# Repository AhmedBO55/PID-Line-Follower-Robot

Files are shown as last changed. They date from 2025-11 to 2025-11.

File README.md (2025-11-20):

# PID Line Follower Robot
##  Project Overview
PID Line Follower Robot is a project with the objective to understand the line follower concept and PID system. It’s an affordable version of a competitive robot, and v0; the next version will have better components and a PCB design.

91e5619f-f241-466d-bc85-fe74e6d3bd5d
---
## Why ?
I did this project because I am very interested in robotics competitions, and I want to create my own line follower robot and compete with it in future competitions. This is why I started this project: to understand the fundamentals before buying fancy components. I decided to make my mistakes now, and I am willing to learn and create a PCB in the future for this project.

{8EE49D31-0FA8-4DDD-9549-9236D85A650A}

68747470733a2f2f626c75657072696e742e6861636b636c75622e636f6d2f757365722d6174746163686d656e74732f626c6f62732f70726f78792f65794a66636d467062484d694f6e73695a474630595349364e7a49774e79776963485679496a6f69596d
---
## Circuit diagram

Circuit diagram

--- 

## Features
- **PID control** for smooth and accurate line following 
- **Real-time PID tuning** via a web page hosted by the robot
- **3D-printed chassis** adapted for the BFD-1000  
- **Bluetooth test mode** for quick motor debugging
  
{E63CA688-48E1-4CCD-8186-648663711028}

---
##  How It Works
1-The BFD-1000 reads the position of the line. 

2-The ESP32 computes an error value from the sensor readings. 

3-A PID algorithm generates the correction output.  

4-The TB6612FNG driver adjusts each motor’s speed. 

5-The robot’s Wi-Fi interface allows live tuning of Kp, Ki, and Kd values. 

---
## BOM (Bill of Materials)
I've created a BOM for the components used in this project. I didn’t include the cost and source links of the vendors, as I live in Tunisia and prices are not like the rest of the world, and our shops are not international.
But I've included the description and notes to explain the use of each component. If you want to change any of them, feel free to do so.

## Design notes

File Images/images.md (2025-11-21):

## 📸 Project Images
--- 
### 🔹 Previous Version (Summer of Making)
68747470733a2f2f626c75657072696e742e6861636b636c75622e636f6d2f757365722d6174746163686d656e74732f626c6f62732f70726f78792f65794a66636d467062484d694f6e73695a474630595349364e6a6b334f43776963485679496a6f69596d

---
### 🔹 Line Follower with QTR Sensor (Old Prototype)

314ee7e9-e2c3-470f-afe7-d1aa61988d41
91e5619f-f241-466d-bc85-fe74e6d3bd5d
68747470733a2f2f626c75657072696e742e6861636b636c75622e636f6d2f757365722d6174746163686d656e74732f626c6f62732f70726f78792f65794a66636d467062484d694f6e73695a474630595349364f446b344f43776963485679496a6f69596d
68747470733a2f2f626c75657072696e742e6861636b636c75622e636f6d2f757365722d6174746163686d656e74732f626c6f62732f70726f78792f65794a66636d467062484d694f6e73695a474630595349364f446b344e79776963485679496a6f69596d
68747470733a2f2f626c75657072696e742e6861636b636c75622e636f6d2f757365722d6174746163686d656e74732f626c6f62732f70726f78792f65794a66636d467062484d694f6e73695a474630595349364e7a63314d43776963485679496a6f69596d
68747470733a2f2f626c75657072696e742e6861636b636c75622e636f6d2f757365722d6174746163686d656e74732f626c6f62732f70726f78792f65794a66636d467062484d694f6e73695a474630595349364e7a63304f53776963485679496a6f69596d
68747470733a2f2f626c75657072696e742e6861636b636c75622e636f6d2f757365722d6174746163686d656e74732f626c6f62732f70726f78792f65794a66636d467062484d694f6e73695a474630595349364e7a63304f43776963485679496a6f69596d

### 🔹 Final Line Follower Robot (With BFD-1000) 

314ee7e9-e2c3-470f-afe7-d1aa61988d41
91e5619f-f241-466d-bc85-fe74e6d3bd5d
b005e480-9caa-4929-82fe-6bf18c532cd6

## 🧩 CAD Models

### 🔹 CAD V1 (Old 3D Model)
{86EB5DD3-BE2E-442E-AB9C-22109B1CB365}

### 🔹 CAD V2 (Updated model for BFD-1000)

{8EE49D31-0FA8-4DDD-9549-9236D85A650A}

## 🔌 Electronics & Circuit
Circuit diagram

68747470733a2f2f626c75657072696e742e6861636b636c75622e636f6d2f757365722d6174746163686d656e74732f626c6f62732f70726f78792f65794a66636d467062484d694f6e73695a474630595349364e7a49774e79776963485679496a6f69596d

68747470733a2f2f626c75657072696e742e6861636b636c75622e636f6d2f757365722d6174746163686d656e74732f626c6f62732f70726f78792f65794a66636d467062484d694f6e73695a474630595349364e7a49774f43776963485679496a6f69596d

5562393c-81c9-4ac4-81d2-6645e74e5eff

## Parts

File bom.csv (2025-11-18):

Item | Description | Quantity | Notes
ESP32 Dev Board | Main microcontroller | 1 | Handles PID
BFD-1000 Line Sensor | 6-channel IR line detection module | 1 | Primary sensor for line following
TB6612FNG Motor Driver | Dual H-bridge motor driver | 1 | Controls both N20 motors with PWM
N20 Gear Motors | 6V DC gear motors | 2 | Main motors for movement
N20 Motor Brackets | 3D printed or metal holders | 2 | Motor mounting
Ball Caster (Bille Libre) | Front support wheel | 1 | Helps robot balance and glide
L7805 Voltage Regulator | 5V linear regulator | 1 | Provides 5V for sensors and logic
Lithium Battery (or 18650 pack) | Main power source | 1 | Used to power motors + electronics
Battery Holder or Case | For securing the battery | 1 | Depending on your battery type
Switch | On/Off power switch | 1 | Main power control
Prototype Board / Custom PCB | Your soldered board or final PCB | 1 | Main circuit assembly
JST / Dupont Cables | Connection wires | As needed | For sensors,motors and power
3D Printed Chassis | Your custom robot frame | 1 | Designed to fit ESP32 + BFD-1000
Wheels | Compatible with N20 motors | 2 | Main driving wheels
Standoffs & Screws | M3 or M2 hardware set | As needed | For assembling chassis and PCB
USB Cable | For flashing ESP32 | 1 | Used during development
Soldering Supplies | Solder,flux,wires | 1 set | For assembling the board

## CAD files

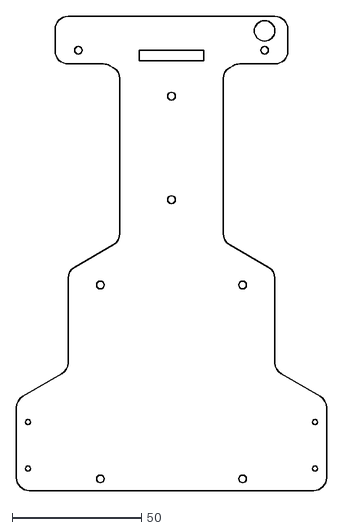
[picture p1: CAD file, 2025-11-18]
CAD/DXF/V2/Line follower robot DXF.dxf
120.0 x 183.4

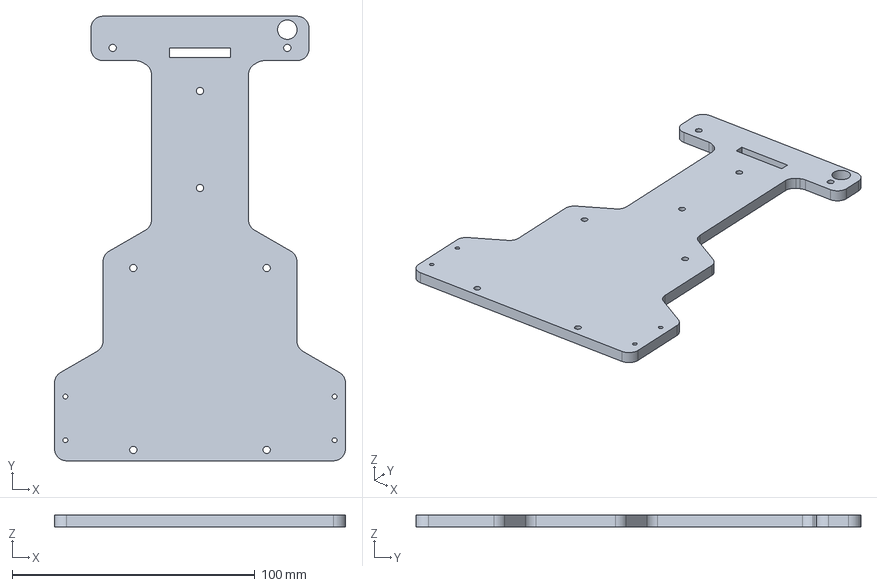
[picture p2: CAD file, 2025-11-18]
CAD/STEP/V2/Line follower robot_.step
120.0 x 183.4 x 5.00 mm

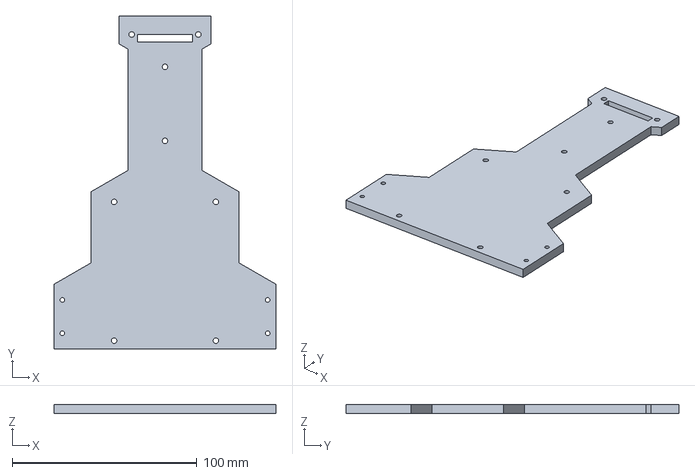
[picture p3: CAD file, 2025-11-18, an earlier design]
CAD/STEP/V1/line follower.step
120.0 x 180.0 x 5.00 mm

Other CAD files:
CAD/DXF/V1/line follower.dxf

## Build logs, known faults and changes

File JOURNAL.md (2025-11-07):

<!--
  ===================    !!READ THIS NOTICE!!   ====================
  DO NOT edit this file manually. Your changes WILL BE OVERWRITTEN!
  This journal is auto generated and updated by Hack Club Blueprint.
  To edit this file, please edit your journal entries on Blueprint.
  ==================================================================
-->

## 10/31/2025 2 PM - My previous work from the Summer of Making.  

This is some of my previous work from the Summer of Making.
I am posting this so as not to count as Blue Print working hours.
What I worked on back then included 3D modeling of the components of the robot as well as the construction of the prototype board using Raspberry Pi Pico. However, the project had not been completed.
Open-Source PID Line Follower (2)

707e0b68-b6ef-40ca-9609-a6343efdecb8

## 10/31/2025 11 PM - New Prototype Board  

Today I built a new prototype and soldered my new board with the ESP32.
It was one of my longest and hardest soldering sessions so far.
The process was quite complex.I had to resolder some parts after realizing I mixed up analog and digital pins for the sensors.
I haven’t tested it with power yet, but I checked continuity with a multimeter, and everything seems connected correctly.
05e07714-f974-4fa2-b5d2-2a651cbbcf54

eb5f2644-13bf-48ca-8c5d-612c822482d7

## 11/2/2025 - Assembly and Motor Testing  

Today, I completed the assembly of the whole robot and spent a great deal of time leveling it, since the wheel diameter, bille libre, and line sensor were not all at the same level. I had to adjust them carefully to everything level out.
Once I was done, I began testing the motors and the TB6612FNG driver. It was my first time using PWM and the enable pins of the TB6612 driver and encountered many small issues, but I got everything worked out as it moved along.
I tested out the motors with the Bluetooth control code and were able to get the motors and TB6612FNG supplier to work properly.
I am still working on getting the QTR sensor to work, so next step is to tackle this.
d8344871-03e9-4145-8de2-d1c7d5ed39c5
ed9c623a-0ca6-4158-a70d-18cbd5404c14
60292b5f-90e8-4e43-bcf8-5e8e3fc0513c

## 11/6/2025 - QTR Testing and Problems Found  

During the last four days, I spent all my time trying to get the QTR sensors to work.
I tested everything using a calibration code and even changed the plate level of the QTR during testing, which helped a bit, but the readings were still unstable.
After many trials, I found that some pins on the QTR sensor and the board were damaged, which caused major signal problems.
Because of that, I’ve decided to replace the QTR sensors with BFD-1000 modules.
This means I’ll need to update my 3D model, adjust the code, and resolder a new board for the new sensors.

245848cd-aa1a-4533-9b5a-98509c06daa58657a45b-9495-46db-8a2a-7735b4af5f6f
9925b78a-51ba-4237-970f-c0037875342b
{2F77CB7B-FFCD-4B57-91C7-A8CAACA83E8E}
`const int pins[8] = {12, 15, 2, 35, 34, 36, 39, 4};
const int total = 8;

int raw[8];
int normalized[8];
int minVal[8];
int maxVal[8];

void setup() {
  Serial.begin(115200);
  delay(1000);
  
  Serial.println("QTR-8A Test");
  Serial.println("===========");
  
  for (int i = 0; i < total; i++) {
    pinMode(pins[i], INPUT);
  }
  
  Serial.println("Pins:");
  for (int i = 0; i < total; i++) {
    Serial.print("S");
    Serial.print(i + 1);
    Serial.print(": ");
    Serial.println(pins[i]);
  }
  Serial.println();
  
  delay(2000);
  runCalibration();
}

void runCalibration() {
  Serial.println("CALIBRATION");
  Serial.println("===========");
  Serial.println("Move sensors over black and white for 5 seconds...");
  Serial.println();
  
  for (int i = 0; i < total; i++) {
    minVal[i] = 4095;
    maxVal[i] = 0;
  }
  
  unsigned long start = millis();
  while (millis() - start < 5000) {
    for (int i = 0; i < total; i++) {
      int val = analogRead(pins[i]);
      
      if (val < minVal[i]) {
        minVal[i] = val;
      }
      if (val > maxVal[i]) {
        maxVal[i] = val;
      }
    }
    
    if ((millis() - start) % 1000 < 50) {
      Serial.print(".");
    }
    delay(10);
  }
  
  Serial.println("\n");
  Serial.println("Done!");
  Serial.println("Range per sensor:");
  
  for (int i = 0; i < total; i++) {
    Serial.print("S");
    Serial.print(i + 1);
    Serial.print(": ");
    Serial.print(minVal[i]);
    Serial.print(" - ");
    Serial.println(maxVal[i]);
  }
  
  Serial.println();
  Serial.println("Readings (0=black, 1000=white)");
  Serial.println("==============================");
  Serial.println();
  delay(2000);
}

void loop() {
  for (int i = 0; i < total; i++) {
    int reading = analogRead(pins[i]);
    raw[i] = reading;
    
    normalized[i] = map(reading, minVal[i], maxVal[i], 0, 1000);
    normalized[i] = constrain(normalized[i], 0, 1000);
  }
  
  Serial.print("Raw:  ");
  for (int i = 0; i < total; i++) {
    Serial.print(raw[i]);
    if (i < total - 1) {
      Serial.print(" | ");
    }
  }
  Serial.println();
  
  Serial.print("Norm: ");
  for (int i = 0; i < total; i++) {
    Serial.print(normalized[i]);
    if (i < total - 1) {
      Serial.print(" | ");
    }
  }
  Serial.println();
  
  Serial.print("View: ");
  for (int i = 0; i < total; i++) {
    int bars = map(normalized[i], 0, 1000, 0, 10);
    for (int j = 0; j < bars; j++) {
      Serial.print("█");
    }
    for (int j = bars; j < 10; j++) {
      Serial.print("·");
    }
    Serial.print(" ");
  }
  Serial.println();
  
  Serial.print("Det:  ");
  for (int i = 0; i < total; i++) {
    if (normalized[i] < 500) {
      Serial.print("■");
    } else {
      Serial.print("□");
    }
    Serial.print(" ");
  }
  Serial.println();
  Serial.println();
  
  delay(200);
}`

## 11/8/2025 - BFD-1000 Soldering and Testing  

Today I started soldering the new board.
I didn’t finish everything yet I only soldered the BFD-1000 module pins.
This time I learned from my previous mistakes, so I decided to test all the sensors before soldering the full board.

Surprisingly, everything worked super well all the sensors are working perfectly and are ready to be used.
The next step will be to finish soldering the entire board and bring the new 3D model to life.
2acf4957-dcae-44c1-afdf-7964abe50abb998227fb-6f2a-42d6-bb61-3794fb786d87

{3020FE48-D0D7-4E40-82B5-0DD504D91152}

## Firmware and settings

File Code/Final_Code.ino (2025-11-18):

#include <WiFi.h>
#include <WebServer.h>

const char* ssid = "Ooredoo-ALHN-05DD";
const char* password = "tEnLxF2D6r";

WebServer server(80);

const int S1 = 33, S2 = 32, S3 = 35, S4 = 34, S5 = 39;
const int PWMA = 18, AIN1 = 16, AIN2 = 17;
const int PWMB = 19, BIN1 = 25, BIN2 = 23, STBY = 5;

const int freqPWM = 1000, resolutionPWM = 8;

int baseSpeed = 180;
int maxSpeed = 240;
int searchSpeed = 60;
float Kp = 18.0, Ki = 0.05, Kd = 22.0;

float lastError = 0, integral = 0;
const float integralLimit = 30.0;
unsigned long lastTime = 0;

const int positions[5] = {-2, -1, 0, 1, 2};
int lastDirection = 0;

volatile bool robotStopped = false;
volatile bool resetRequested = false;

int stuckCounter = 0;
const int stuckThreshold = 8;

const char webpage[] PROGMEM = R"rawliteral(
<!DOCTYPE html>
<html>
<head>
<meta name="viewport" content="width=device-width, initial-scale=1">
<title>Line Control</title>
<style>
body{font-family:Arial;background:#667eea;padding:20px;margin:0}
.container{max-width:500px;margin:0 auto;background:#fff;border-radius:10px;padding:25px}
h1{color:#667eea;text-align:center;margin-bottom:20px}
.section{background:#f5f5f5;padding:15px;border-radius:8px;margin-bottom:15px}
.section h2{font-size:16px;margin:0 0 10px 0;color:#333}
.group{margin:10px 0}
label{display:block;font-weight:bold;margin-bottom:3px;font-size:14px}
input{width:100%;padding:8px;border:1px solid #ddd;border-radius:4px;font-size:14px}
.btn{width:100%;padding:12px;border:none;border-radius:6px;font-size:16px;font-weight:bold;cursor:pointer;margin-top:8px}
.btn-primary{background:#667eea;color:#fff}
.btn-danger{background:#e74c3c;color:#fff}
</style>
</head>
<body>
<div class="container">
<h1>Line Follower</h1>
<div class="section">
<h2>Speed</h2>
<div class="group">
<label>Base:</label>
<input type="number" id="baseSpeed" value="85" min="0" max="255">
</div>
<div class="group">
<label>Max:</label>
<input type="number" id="maxSpeed" value="110" min="0" max="255">
</div>
<div class="group">
<label>Search:</label>
<input type="number" id="searchSpeed" value="60" min="0" max="255">
</div>
</div>
<div class="section">
<h2>PID</h2>
<div class="group">
<label>Kp:</label>
<input type="number" id="kp" value="18.0" step="0.1">
</div>
<div class="group">
<label>Ki:</label>
<input type="number" id="ki" value="0.05" step="0.01">
</div>
<div class="group">
<label>Kd:</label>
<input type="number" id="kd" value="22.0" step="0.1">
</div>
</div>
<button class="btn btn-primary" onclick="apply()">Apply</button>
<button class="btn btn-danger" onclick="reset()">Reset</button>
</div>
<script>
function apply(){
const p=new URLSearchParams({
baseSpeed:document.getElementById('baseSpeed').value,
maxSpeed:document.getElementById('maxSpeed').value,
searchSpeed:document.getElementById('searchSpeed').value,
kp:document.getElementById('kp').value,
ki:document.getElementById('ki').value,
kd:document.getElementById('kd').value
});
fetch('/update?'+p.toString()).then(r=>r.text()).then(()=>alert('Applied'));
}
function reset(){
if(confirm('Reset?')){
fetch('/reset').then(()=>{alert('Resetting...');setTimeout(()=>location.reload(),2000);});
}
}
</script>
</body>
</html>
)rawliteral";

void setup() {
  Serial.begin(115200);
  delay(500);
  
  Serial.println("\nStarting...");
  
  pinMode(S1, INPUT); pinMode(S2, INPUT); pinMode(S3, INPUT);
  pinMode(S4, INPUT); pinMode(S5, INPUT);
  pinMode(AIN1, OUTPUT); pinMode(AIN2, OUTPUT);
  pinMode(BIN1, OUTPUT); pinMode(BIN2, OUTPUT); pinMode(STBY, OUTPUT);
  
  digitalWrite(AIN1, LOW); digitalWrite(AIN2, LOW);
  digitalWrite(BIN1, LOW); digitalWrite(BIN2, LOW);
  digitalWrite(STBY, LOW);
  
  ledcAttach(PWMA, freqPWM, resolutionPWM);
  ledcAttach(PWMB, freqPWM, resolutionPWM);
  ledcWrite(PWMA, 0); ledcWrite(PWMB, 0);
  
  digitalWrite(STBY, HIGH);
  
  Serial.print("Connecting to: ");
  Serial.println(ssid);
  
  WiFi.begin(ssid, password);
  int attempts = 0;
  while (WiFi.status() != WL_CONNECTED && attempts < 40) {
    delay(500);
    Serial.print(".");
    attempts++;
  }
  
  Serial.println();
  
  if (WiFi.status() == WL_CONNECTED) {
    Serial.println("Connected!");
    Serial.print("IP: ");
    Serial.println(WiFi.localIP());
  } else {
    Serial.println("WiFi failed!");
  }
  
  server.on("/", HTTP_GET, []() {
    server.send(200, "text/html", webpage);
  });
  
  server.on("/update", HTTP_GET, handleUpdate);
  server.on("/reset", HTTP_GET, handleReset);
  
  server.begin();
  Serial.println("Server started");
  
  delay(2000);
}

void loop() {
  server.handleClient();
  
  if (resetRequested) {
    ESP.restart();
  }
  
  if (!robotStopped) {
    followLine();
  }
  
  delay(10);
}

void followLine() {
  int s1 = !digitalRead(S1), s2 = !digitalRead(S2), s3 = !digitalRead(S3);
  int s4 = !digitalRead(S4), s5 = !digitalRead(S5);
  
  if (s1 && s2 && s3 && s4 && s5) {
    stopRobot();
    return;
  }
  
  if (!s1 && !s2 && !s3 && !s4 && !s5) {
    searchForLine();
    stuckCounter++;
    if (stuckCounter > stuckThreshold) {
      setMotorSpeed(baseSpeed, baseSpeed);
      stuckCounter = 0;
    }
    return;
  }
  
  stuckCounter = 0;
  
  float error = calculateError(s1, s2, s3, s4, s5);
  
  if (error < -0.5) lastDirection = -1;
  else if (error > 0.5) lastDirection = 1;
  
  unsigned long currentTime = millis();
  float dt = (currentTime - lastTime) / 1000.0;
  
  if (lastTime == 0 || dt > 1.0) {
    lastTime = currentTime;
    dt = 0.01;
  }
  
  if (dt > 0) {
    float P = Kp * error;
    
    integral += error * dt;
    integral = constrain(integral, -integralLimit, integralLimit);
    float I = Ki * integral;
    
    float derivative = (error - lastError) / dt;
    float D = Kd * derivative;
    
    float correction = P + I + D;
    
    if (s3 == 1 && abs(error) < 0.5) {
      correction *= 0.2;
      integral *= 0.5;
    }
    
    int leftSpeed = constrain(baseSpeed + correction, -maxSpeed, maxSpeed);
    int rightSpeed = constrain(baseSpeed - correction, -maxSpeed, maxSpeed);
    
    setMotorSpeed(leftSpeed, rightSpeed);
    
    lastError = error;
    lastTime = currentTime;
  }
}

void searchForLine() {
  int leftSpeed = (lastDirection <= 0) ? -searchSpeed : searchSpeed;
  int rightSpeed = -leftSpeed;
  setMotorSpeed(leftSpeed, rightSpeed);
}

void stopRobot() {
  digitalWrite(AIN1, LOW); digitalWrite(AIN2, LOW);
  digitalWrite(BIN1, LOW); digitalWrite(BIN2, LOW);
  ledcWrite(PWMA, 0); ledcWrite(PWMB, 0);
  robotStopped = true;
}

float calculateError(int s1, int s2, int s3, int s4, int s5) {
  int sensors[5] = {s1, s2, s3, s4, s5};
  float weightedSum = 0;
  int sensorCount = 0;
  
  for (int i = 0; i < 5; i++) {
    if (sensors[i] == 1) {
      weightedSum += positions[i];
      sensorCount++;
    }
  }
  
  return (sensorCount == 0) ? lastError : weightedSum / sensorCount;
}

void setMotorSpeed(int leftSpeed, int rightSpeed) {
  if (leftSpeed > 0) {
    digitalWrite(AIN1, HIGH); digitalWrite(AIN2, LOW);
  } else if (leftSpeed < 0) {
    digitalWrite(AIN1, LOW); digitalWrite(AIN2, HIGH);
  } else {
    digitalWrite(AIN1, LOW); digitalWrite(AIN2, LOW);
  }
  ledcWrite(PWMA, abs(leftSpeed));
  
  if (rightSpeed > 0) {
    digitalWrite(BIN1, LOW); digitalWrite(BIN2, HIGH);
  } else if (rightSpeed < 0) {
    digitalWrite(BIN1, HIGH); digitalWrite(BIN2, LOW);
  } else {
    digitalWrite(BIN1, LOW); digitalWrite(BIN2, LOW);
  }
  ledcWrite(PWMB, abs(rightSpeed));
}

void handleUpdate() {
  if (server.hasArg("baseSpeed")) baseSpeed = server.arg("baseSpeed").toInt();
  if (server.hasArg("maxSpeed")) maxSpeed = server.arg("maxSpeed").toInt();
  if (server.hasArg("searchSpeed")) searchSpeed = server.arg("searchSpeed").toInt();
  if (server.hasArg("kp")) Kp = server.arg("kp").toFloat();
  if (server.hasArg("ki")) Ki = server.arg("ki").toFloat();
  if (server.hasArg("kd")) Kd = server.arg("kd").toFloat();
  
  server.send(200, "text/plain", "OK");
}

void handleReset() {
  server.send(200, "text/plain", "Resetting");
  delay(100);
  resetRequested = true;
}

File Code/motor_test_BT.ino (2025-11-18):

#include <BluetoothSerial.h>

#if !defined(CONFIG_BT_ENABLED) || !defined(CONFIG_BLUEDROID_ENABLED)
#error Bluetooth is not enabled! Please run `make menuconfig` and enable it
#endif

BluetoothSerial SerialBT;

const int PWMA = 18;
const int AIN1 = 16;
const int AIN2 = 17;

const int PWMB = 19;
const int BIN1 = 25;
const int BIN2 = 23;
const int STBY = 5;

const int freqPWM = 1000;
const int resolutionPWM = 8;

int currentSpeed = 200; 
char currentCommand = 'S'; 

void setup() {
  Serial.begin(115200);
  Serial.println("\n=== ESP32 Car Ready ===");
  
  pinMode(AIN1, OUTPUT);
  pinMode(AIN2, OUTPUT);
  pinMode(BIN1, OUTPUT);
  pinMode(BIN2, OUTPUT);
  pinMode(STBY, OUTPUT);
  
  digitalWrite(AIN1, LOW);
  digitalWrite(AIN2, LOW);
  digitalWrite(BIN1, LOW);
  digitalWrite(BIN2, LOW);
  digitalWrite(STBY, LOW);
  
  delay(100);
  
  ledcAttach(PWMA, freqPWM, resolutionPWM);
  ledcAttach(PWMB, freqPWM, resolutionPWM);
  
  ledcWrite(PWMA, 0);
  ledcWrite(PWMB, 0);
  
  digitalWrite(STBY, HIGH);
  
  SerialBT.begin("ESP32_Car");
  Serial.println("BT: ESP32_Car");
  Serial.println("Waiting for connection...\n");
}

void loop() {
  if (SerialBT.available()) {
    char cmd = SerialBT.read();
    handleCommand(cmd);
  }
  
  if (Serial.available()) {
    char cmd = Serial.read();
    handleCommand(cmd);
  }
}

void handleCommand(char cmd) {
  cmd = toupper(cmd);
  
  if (cmd >= '0' && cmd <= '9') {
    int level = cmd - '0';
    currentSpeed = map(level, 0, 9, 0, 255);
    Serial.print("Speed: ");
    Serial.print(level);
    Serial.print(" (");
    Serial.print(currentSpeed);
    Serial.println("/255)");
    SerialBT.print("Speed: ");
    SerialBT.println(level);
    return;
  }
  
  currentCommand = cmd;
  
  switch(cmd) {
    case 'F':
      moveForward();
      Serial.println(">> Forward");
      SerialBT.println("Forward");
      break;
      
    case 'B':
      moveBackward();
      Serial.println(">> Back");
      SerialBT.println("Back");
      break;
      
    case 'L':
      turnLeft();
      Serial.println(">> Left");
      SerialBT.println("Left");
      break;
      
    case 'R':
      turnRight();
      Serial.println(">> Right");
      SerialBT.println("Right");
      break;
      
    case 'G':
      forwardLeft();
      Serial.println(">> Fwd-Left");
      SerialBT.println("Fwd-Left");
      break;
      
    case 'I':
      forwardRight();
      Serial.println(">> Fwd-Right");
      SerialBT.println("Fwd-Right");
      break;
      
    case 'H':
      backwardLeft();
      Serial.println(">> Back-Left");
      SerialBT.println("Back-Left");
      break;
      
    case 'J':
      backwardRight();
      Serial.println(">> Back-Right");
      SerialBT.println("Back-Right");
      break;
      
    case 'S':
      stopMotors();
      Serial.println(">> Stop");
      SerialBT.println("Stop");
      break;
      
    default:
      Serial.print("Unknown: ");
      Serial.println(cmd);
      break;
  }
}

void moveForward() {
  digitalWrite(AIN1, HIGH);
  digitalWrite(AIN2, LOW);
  ledcWrite(PWMA, currentSpeed);
  
  digitalWrite(BIN1, LOW);
  digitalWrite(BIN2, HIGH);
  ledcWrite(PWMB, currentSpeed);
}

void moveBackward() {
  digitalWrite(AIN1, LOW);
  digitalWrite(AIN2, HIGH);
  ledcWrite(PWMA, currentSpeed);
  
  digitalWrite(BIN1, HIGH);
  digitalWrite(BIN2, LOW);
  ledcWrite(PWMB, currentSpeed);
}

void turnLeft() {
  digitalWrite(AIN1, LOW);
  digitalWrite(AIN2, HIGH);
  ledcWrite(PWMA, currentSpeed);
  
  digitalWrite(BIN1, LOW);
  digitalWrite(BIN2, HIGH);
  ledcWrite(PWMB, currentSpeed);
}

void turnRight() {
  digitalWrite(AIN1, HIGH);
  digitalWrite(AIN2, LOW);
  ledcWrite(PWMA, currentSpeed);
  
  digitalWrite(BIN1, HIGH);
  digitalWrite(BIN2, LOW);
  ledcWrite(PWMB, currentSpeed);
}

void forwardLeft() {
  digitalWrite(AIN1, HIGH);
  digitalWrite(AIN2, LOW);
  ledcWrite(PWMA, currentSpeed / 2);
  
  digitalWrite(BIN1, LOW);
  digitalWrite(BIN2, HIGH);
  ledcWrite(PWMB, currentSpeed);
}

void forwardRight() {
  digitalWrite(AIN1, HIGH);
  digitalWrite(AIN2, LOW);
  ledcWrite(PWMA, currentSpeed);
  
  digitalWrite(BIN1, LOW);
  digitalWrite(BIN2, HIGH);
  ledcWrite(PWMB, currentSpeed / 2);
}

void backwardLeft() {
  digitalWrite(AIN1, LOW);
  digitalWrite(AIN2, HIGH);
  ledcWrite(PWMA, currentSpeed / 2);
  
  digitalWrite(BIN1, HIGH);
  digitalWrite(BIN2, LOW);
  ledcWrite(PWMB, currentSpeed);
}

void backwardRight() {
  digitalWrite(AIN1, LOW);
  digitalWrite(AIN2, HIGH);
  ledcWrite(PWMA, currentSpeed);
  
  digitalWrite(BIN1, HIGH);
  digitalWrite(BIN2, LOW);
  ledcWrite(PWMB, currentSpeed / 2);
}

void stopMotors() {
  digitalWrite(AIN1, LOW);
  digitalWrite(AIN2, LOW);
  digitalWrite(BIN1, LOW);
  digitalWrite(BIN2, LOW);
  ledcWrite(PWMA, 0);
  ledcWrite(PWMB, 0);
}

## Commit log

2025-11-18 Add initial content to CAD/DXF/D file
2025-11-18 Revise README with project details and features
    Updated README to provide a detailed project overview and features of the PID Line Follower Robot.
2025-11-21 Update project images and CAD model sections
    Added images and CAD models for various project components.
